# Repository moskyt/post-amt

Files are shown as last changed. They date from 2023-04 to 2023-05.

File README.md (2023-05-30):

# POSTAMT

Darek pro Vlka a Vorsilu k narozeninam 2023.

Obecne: posledni tyden provazela hardwarova dramata a tak je SW mirne nedotazeny. Urceno k libovolnym upravam chovani i implementace podle potreby a aktualnich napadu.

## Hardware

### Komponenty

#### mainboard

Arduino Nano Every (5V)

nevim proc a nemel jsem prostor na dalsi zkoumani, ale pokud je pripojeny zdroj do site, tak se mi nedari pripojit pres usb.

#### zdroj - 5+12

MEANWELL RD 35A
https://www.gme.cz/v/1506286/mean-well-rd-35a-spinany-zdroj-pro-vestavbu-kryty

tepdown z 12 na 8.5v pro tiskarnu
https://www.laskakit.cz/mikro-step-down-menic--nastavitelny

#### bzucak

aktivni 5v bzucak

#### ciselnik

vykuchany rotacni ciselnik z telefonu
https://aukro.cz/ciselnik-telefonu-zcela-funkcni-9x4-cm-7034546220

#### LCD 

znakovy LCD 20x4 s i2c
https://www.laskakit.cz/20x4-lcd-displej-2004-modry-i2c-prevodnik/

#### vaha

trikilogramovy vahovy senzor
https://www.laskakit.cz/guang-ce-yzc-131-vazici-senzor-3kg/
https://www.laskakit.cz/ad-prevodnik-modul-24-bit-2-kanaly-hx711/

#### led displej pro vahu

4-digit 8-segment
https://www.laskakit.cz/hodinovy-displej-0-56--tm1637/

#### RFID ctecka -- RC522 / 13.56 MHz

https://www.laskakit.cz/rfid-ctecka-s-vestavenou-antenou-mfrc-522-rc522/

#### zamek

https://www.laskakit.cz/elektromagneticky-zamek-pro-dvere-12vdc-0-6a/

pres mosfet
https://www.laskakit.cz/pwm-mosfet-modul-lr7843--30vdc-161a/

#### tiskarna

https://www.adafruit.com/product/597

#### klavesnice

NeoKey
https://www.adafruit.com/product/4980

### Zapojeni

#### Piny z Arduina

2+3 - vaha (data, clk)
4 - bzucak
5 - rotacni ciselnik
7+8 - led (clk, data)
9+10 - rfid (ss, rst)
16+17 - tiskarna (rx, tx)
18+19 - I2C (neokey, LCD)
20 - zamek pres mosfet

#### Pripojeni komponent na mainboard

R32-35 vaha[GND,DATA,CLK,VCC]
? bzucak[+,GND]
R27-28 rotacni ciselnik[*,*]
R38-41 led[VCC,GND,DATA,CLK]
L23-20 lcd[GND,VCC,SDA,SCL]
L36-34 tiskarna[?,?,GND]
L45-38 rfid[3v3,?,GND,?,MISO,?,SCK,SS]
L30-27 neokey[VCC,GND,SCL,SDA]

zamek -- do svorkovnice na mosfetu

5v napajeni -- do svorkovnice na mainboardu
12v napajeni -- do wago svorek

#### 12V komponenty

mosfet pro zamek

napajeni pro tiskarnu (stepdown na 8.5VÎ)

## Funkce

### Vaha

po zatizeni se ukaze hmotnost

pokud neprobiha odesilani zasilek, lze tlacitkem vynulovat taru

### Odesilani zasilek

po navazeni vybiram tlacitkem balik nebo dopis

na LCD se mi ukaze pridana zasilka a pocet zasilek

tlacitkem vsechno vyresetuju

tlacitkem zahajim odesilani

po prilozeni karty se vytiskne listecek

### Suplik

po vytoceni kodu 1234 se otevre

zapadka: vzadu shora

automaticke otevirani na odpuzujici se magnety vedlo k tomu, ze se zapadka nedokazala otevrit (tlak zboku - vysoke treni nebo se to rovnou zkrizilo). nestihnul jsem vyzkouset ruzne alternativy, ale mozna by to spravne slaba pruzina nebo spravna dvojice magnetu vyresila.

--- na posledni chvili jsem zkusil dat tam dvojici slabsich magnetu a obecne to funguje skvele, ale uz se mi taky stalo, ze se to odmitlo otevrit. tak nevim, je asi potreba posoudit provozni zkusenost. kdyztak proste staci vyndat jeden magnet a je to. nejaky automatizovany chytroreseni by vyzadovalo koncovej spinac a dat tomu vic pokusu, ale to bylo nad aktualni ramec moznosti.

## Software

jako obvykle to vznikalo v prvni fazi dlouho a v druhe fazi narychlo a urcite nema nikdo nic proti zasadnim i drobnym zmenam.

neni tam asi nic nestandardniho, snad jen ten timer pro asynchronni reseni toho rotacniho ciselniku. 

### Logo Die Post na tiskarnu

pouzil jsem postup z https://learn.adafruit.com/mini-thermal-receipt-printer/bitmap-printing

ten skript je v adresari grafika taky

## Playware

nejaky bizar z aukra

par osvojenych formularu z ceske posty

pokud mi bude sihlpost milostiv, tak https://shop.post.ch/shop/ui/de/geschenke/spielwaren/kinderpost-zubehor/p/507512

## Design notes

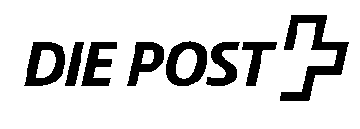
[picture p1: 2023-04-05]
grafika/die_post_360.png

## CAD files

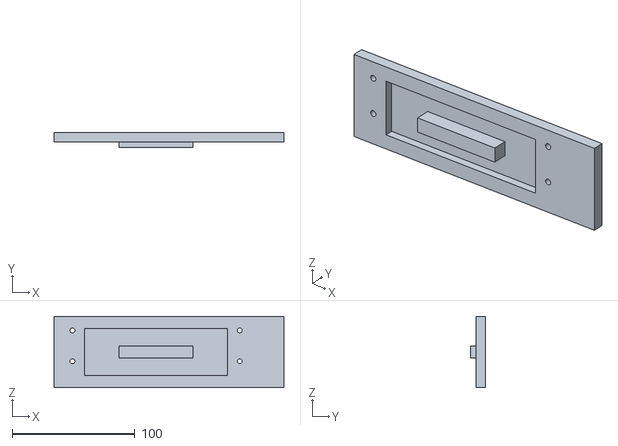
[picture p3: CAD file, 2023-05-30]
grafika/postamt_front_drawer.stl
187.0 x 12.0 x 58.0

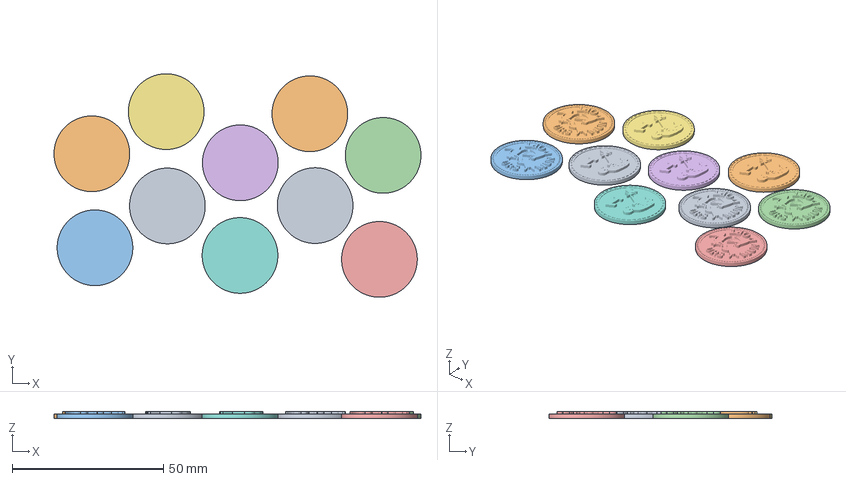
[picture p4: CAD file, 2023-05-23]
grafika/mince v4.3mf
121.2 x 73.8 x 2.20 mm

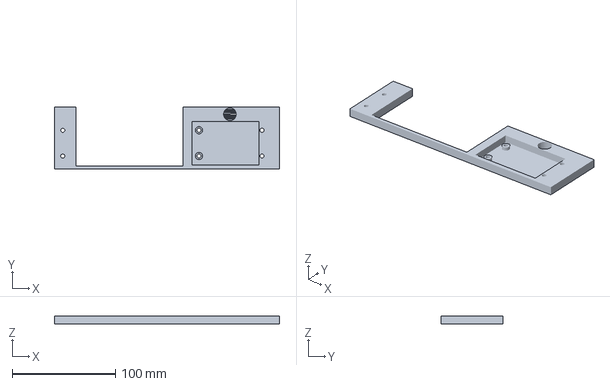
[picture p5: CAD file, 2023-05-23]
grafika/postamt_front_module.3mf
218.0 x 60.0 x 7.50 mm

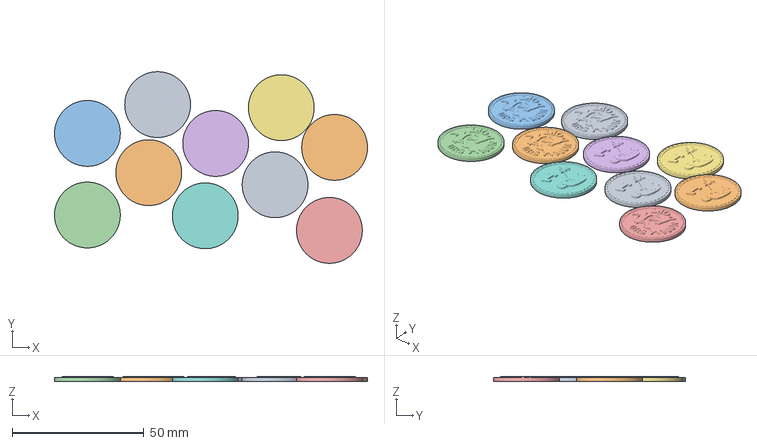
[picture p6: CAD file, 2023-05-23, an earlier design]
grafika/mince v2.3mf
118.9 x 72.8 x 2.00 mm

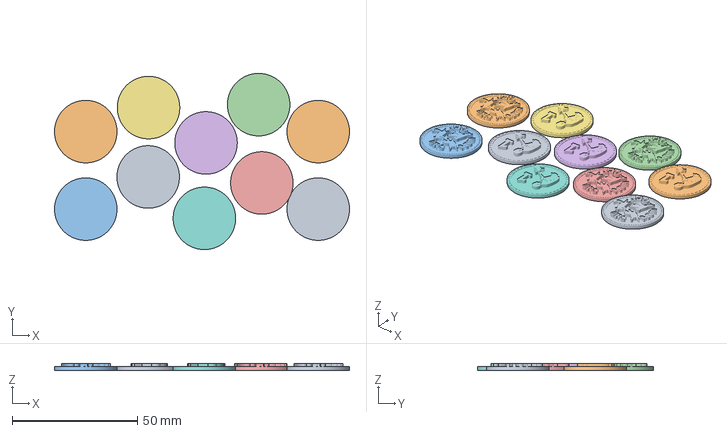
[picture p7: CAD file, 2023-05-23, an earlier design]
grafika/mince v3.3mf
118.0 x 70.5 x 2.60 mm

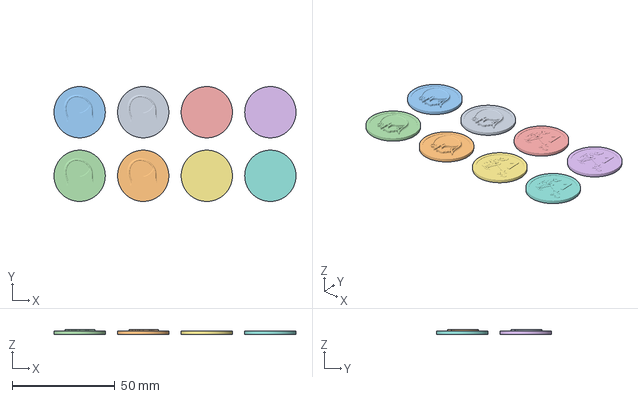
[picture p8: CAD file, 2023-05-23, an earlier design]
grafika/mince v1.3mf
118.0 x 56.0 x 2.20 mm

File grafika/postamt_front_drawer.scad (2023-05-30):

include <bosl2/std.scad>
$fn = 80;

eps = 0.01;

total_z = 7.5;
total_y = 58;
total_x = 187;
roffset_x1 = 36;
roffset_x2 = 172;

printer_x = 103.5;
printer_y = 57;

rfid_up = 13;

difference() {
    cuboid([total_x,total_z,total_y], anchor = BOTTOM+RIGHT+FWD);

    fwd(eps)
    up(rfid_up+1) {

    left(roffset_x1)
    union() {
        up(7.5)
        ycyl(d = 4, l = total_z+2*eps, anchor = FWD);
        up(32.5)
        ycyl(d = 4, l = total_z+2*eps, anchor = FWD);    
    }

    left(roffset_x2)
    union() {
        up(7.5)
        ycyl(d = 4, l = total_z+2*eps, anchor = FWD);
        up(32.5)
        ycyl(d = 4, l = total_z+2*eps, anchor = FWD);
    }
    }

    fwd(eps)
    up(10)
    left(roffset_x1+10)
    cuboid([roffset_x2-roffset_x1-20,total_z-2+eps,total_y-20], anchor = BOTTOM+RIGHT+FWD);

}

back(eps+total_z-2)
left(roffset_x1 + (roffset_x2-roffset_x1)/2)
up(total_y/2)
cuboid([60,10+eps,10], anchor = BACK);

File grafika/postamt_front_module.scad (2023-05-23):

include <bosl2/std.scad>
$fn = 80;

eps = 0.01;

total_z = 7.5;
total_y = 60;

printer_lip_x = 5;
board_left = 16;

printer_x = 103.5;
printer_y = 57;

rfid_up = 14;

difference() {
    union() {
        difference() {
            cuboid([218,total_z,total_y], anchor = BOTTOM+LEFT+FWD);

            right(board_left+printer_lip_x)
            fwd(eps)
            down(eps)
            cuboid([printer_x,total_z+eps*2,printer_y+eps], anchor = BOTTOM+LEFT+FWD);
            
            right(133)
            up(rfid_up)
            back(1)
            cuboid([65,total_z,42], anchor = BOTTOM+LEFT+FWD);
        }    
        right(133+1+6)
        union() {
            up(rfid_up+1+7.5)
            ycyl(d = 7, l = 4, anchor = FWD);
            up(rfid_up+1+32.5)
            ycyl(d = 7, l = 4, anchor = FWD);
        }
    }

    fwd(eps-1)
    right(170)
    up(7)
    ycyl(d = 12.2, l = total_z+2*eps, anchor = FWD);

    fwd(eps)
    right(170)
    up(7)
    intersection() {
       ycyl(d = 12.2, l = total_z+2*eps, anchor = FWD);
       fwd(eps)
        zcopies(2,5)
       cuboid([16,16,1+2*eps], anchor = FWD);

    }

    fwd(eps)
    up(rfid_up+1) {
    right(board_left/2)
    union() {
        up(7.5)
        ycyl(d = 4, l = total_z+2*eps, anchor = FWD);
        up(32.5)
        ycyl(d = 4, l = total_z+2*eps, anchor = FWD);
    }

    right(201)
    union() {
        up(7.5)
        ycyl(d = 4, l = total_z+2*eps, anchor = FWD);
        up(32.5)
        ycyl(d = 4, l = total_z+2*eps, anchor = FWD);
    }

    right(133+1+6)
    union() {
        up(7.5)
        ycyl(d = 4, l = total_z+2*eps, anchor = FWD);
        up(32.5)
        ycyl(d = 4, l = total_z+2*eps, anchor = FWD);
    }
}
}

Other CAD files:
grafika/postamt_front_module.stl

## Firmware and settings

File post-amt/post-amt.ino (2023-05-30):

#include "Adafruit_Thermal.h"
#include "Adafruit_NeoKey_1x4.h"
#include "seesaw_neopixel.h"
#include "SoftwareSerial.h"
#include <Wire.h>
#include <hd44780.h>                      
#include <hd44780ioClass/hd44780_I2Cexp.h>
#include <MFRC522v2.h>
#include <MFRC522DriverSPI.h>
#include <MFRC522DriverPinSimple.h>
#include <MFRC522Debug.h>
#include <HX711_ADC.h>
#include <TM1637Display.h>
#include "die_post_360.h"

//--- pins and adresses

const int I2C_LCD = 0x27;
const int I2C_NEOKEY = 0x30;

const int PIN_LOAD_DATA = 2;
const int PIN_LOAD_CLK = 3;
const int PIN_BEEP = 4;
const int PIN_DIAL = 5;
const int PIN_LED_DATA = 7;
const int PIN_LED_CLK = 8;
const int PIN_RFID_RST = 9;
const int PIN_RFID_SS  = 10;
const int PIN_PRINTER_TX = 16;
const int PIN_PRINTER_RX = 17;
const int PIN_LOCK = 20;
const int PIN_ROTARY = 21;

//--- RFID card ids
const unsigned long int UID_VLK     = 0x9763D21E;
const unsigned long int UID_VORSILA = 0x5B693E3A;

//--- neokey functional assignment
const int BTN_ADD_PARCEL = 0;
const int BTN_ADD_LETTER = 1;
const int BTN_SEND = 2;
const int BTN_RESET = 3;
const int BTN_TARE = 3;

//--- configuration
const float load_cell_cal = 733.0; // this should be acquired from the calibration script; it is available as an example in the HX711_ADC library
const int min_load = 2;
const int scale_zero_weight_timeout = 5000;
const int correct_code = 1234;

//--- hw components

// RFID reader
MFRC522DriverPinSimple ss_pin(PIN_RFID_SS);
SPIClass &spiClass = SPI;
const SPISettings spiSettings = SPISettings(SPI_CLOCK_DIV4, MSBFIRST, SPI_MODE0); 
MFRC522DriverSPI driver{ss_pin, spiClass, spiSettings};
MFRC522 mfrc522{driver};

// LCD display
hd44780_I2Cexp lcd(I2C_LCD);

// LED display
TM1637Display led(PIN_LED_CLK, PIN_LED_DATA);

// neokey 4-button leopard
Adafruit_NeoKey_1x4 neokey;

// 3kg load cell with HX711
HX711_ADC loadcell(PIN_LOAD_DATA, PIN_LOAD_CLK);

//
SoftwareSerial printerSerial(PIN_PRINTER_RX, PIN_PRINTER_TX);
Adafruit_Thermal printer(&printerSerial);

//--- state management

enum shipment_type_ {SHIPMENT_TYPE_NONE, SHIPMENT_TYPE_PARCEL, SHIPMENT_TYPE_LETTER};

enum scale_state_ {SCALE_OFF, SCALE_ON} scale_state;

enum shipping_state_ {SHIPPING_COLLECTION, SHIPPING_CARD, SHIPPING_PRINTING} shipping_state;

int scale_weight = 0;
int shipment_count = 0;
const int max_shipment_count = 5;
int shipment_weight[max_shipment_count];
shipment_type_ shipment_type[max_shipment_count];

// global time at beginning of loop()
unsigned long now = 0;
// flag register of the neokey 
uint8_t buttons = 0;

// timers stuff -- taken from the library

// Select USING_16MHZ     == true for  16MHz to Timer TCBx => shorter timer, but better accuracy
// Select USING_8MHZ      == true for   8MHz to Timer TCBx => shorter timer, but better accuracy
// Select USING_250KHZ    == true for 250KHz to Timer TCBx => shorter timer, but better accuracy
// Not select for default 250KHz to Timer TCBx => longer timer,  but worse accuracy
#define USING_16MHZ     false
#define USING_8MHZ      false
#define USING_250KHZ    false

// Select the timers you're using, here ITimer1
#define USE_TIMER_0     false
#define USE_TIMER_1     true
#define USE_TIMER_2     false
#define USE_TIMER_3     false

#include "megaAVR_TimerInterrupt.h"

// --- dial stuff
// last value read
int dialLastVal = -1;
// timer/counter
int dialCount = 0;
// current number being read
int dialBuffer = 0;
// number of digits in code
const int dialNMax = 4;
// current code read
int dialNumber[dialNMax] = {0,0,0,0};
// current digit
int dialPtr = 0;

// what is available after init
// the idea here is that if neokey is not connected, any call results in reset
bool neokey_available = false;
bool rfid_available = false;

// what is currently read
// remember that 0 is a valid value for dial...
int dial_read = -1;
unsigned long card_read = -1;

// what is shown and when
int show_dial = -1;
unsigned long show_card = 0;
unsigned long int show_card_at = 0;
unsigned long int show_dial_at = 0;
const int show_delay = 10000; // actual ms

void loop() {

  now = millis();

  // read keyboard status
  if (neokey_available)
    buttons = neokey.read();

  // flag to show if any of the keyboard data was set
  // give me credit for this not being a global variable
  bool any_info_neo = false;
  if (neokey_available)
    for (uint16_t i=0; i<neokey.pixels.numPixels(); i++) 
      neokey.pixels.setPixelColor(i, 0x000000);

  if (rfid_available) read_rfid();
  display_scale_led();
  get_weight_from_scale();

  // waiting for card before sending?
  if (shipping_state == SHIPPING_CARD) 
    if ( (card_read == UID_VLK) || (card_read == UID_VORSILA) ) 
      print_shipment(card_read);

  // disable ux if printing the receipt
  if (neokey_available)
  if (shipping_state == SHIPPING_PRINTING) {    
    any_info_neo = true;
    for (uint16_t i=0; i<neokey.pixels.numPixels(); i++) 
      neokey.pixels.setPixelColor(i, 0xFF8888);    
  }

  if (shipment_count == 0)
    // allow tare setting if no shipping is in progress
    handle_tare(any_info_neo);
  else
    // handle finalization of shipping process (reset or proceed with sending)
    reset_or_send(any_info_neo);  

  // process adding a new item
  add_shipments(any_info_neo);

  // (de)queue other info for show
  if (show_dial > 0) {
    if (show_dial_at + show_delay < now) {
      show_dial = -1;
      show_dial_at = 0;
    }
  } 
  if (dial_read >= 0 && show_dial != dial_read) {
    show_dial = dial_read;
    show_dial_at = now;
  }
  if (show_card > 0) {
    if (show_card_at + show_delay < now) {
      show_card = 0;
      show_card_at = 0;
    }
  } 
  if (card_read > 0 && show_card != card_read) {
    show_card = card_read;
    show_card_at = now;
  }


  if (shipment_count > 0 || show_card_at > 0 || show_dial_at > 0) 
    lcd.backlight();

  if (show_card_at == now && (show_dial_at == 0 || show_card_at > show_dial_at)) {
    lcd.setCursor(0,2);
    lcd.print(F("KARTA:               "));
    lcd.setCursor(0,3);
    if (show_card == UID_VORSILA) 
      lcd.print(F("VORSILA             "));
    else if (show_card == UID_VLK) 
      lcd.print(F("VLK                 "));
    else
      lcd.print(show_card, HEX);
  } else if (show_dial_at == now) {
    lcd.setCursor(0,2);
    lcd.print(F("KOD ZAMKU:"));
    lcd.setCursor(0,3);
    if (show_dial < 1000) lcd.print(F("0"));
    if (show_dial < 100) lcd.print(F("0"));
    if (show_dial < 10) lcd.print(F("0"));
    lcd.print(show_dial);
  }
  
  // clear shipping info
  if (shipment_count == 0) lcd_clear_top();
  // clear card/dial info
  if ((show_card_at == 0) && (show_dial_at == 0)) lcd_clear_bottom();

  // shut off lcd if there is nothing going on
  if ( (shipment_count == 0) && (show_dial_at == 0) && (show_card_at == 0) ) {
    lcd.noBacklight();
    lcd.clear();
  }

  if (neokey_available) {
    // show pixels: either just use pale white or whatever was set by the ux
    if (!any_info_neo) 
      for (uint16_t i=0; i<neokey.pixels.numPixels(); i++) 
        neokey.pixels.setPixelColor(i, 0x333333);
    neokey.pixels.show();    
  }

  // unlock
  if (dial_read >= 0) {
    Serial.print(F("dial: "));
    Serial.println(dial_read);
    if (dial_read == correct_code) {
      dial_read = -1;
      Serial.println(F("Unlocking."));
      digitalWrite(PIN_LOCK, HIGH);
      delay(1000);
      digitalWrite(PIN_LOCK, LOW);
    } else {
      Serial.println(F("Code not correct."));
      beep1(500);
    }
    dial_read = -1;
  }

  // any delay is inherently bad, maybe we can refactor this to use timers. but...
  delay(50);
}

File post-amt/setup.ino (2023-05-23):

void setup() {
  // ---
  Serial.begin(115200);
  while (! Serial) delay(10);
  Serial.println(F("PostAmt HELO\n"));  

  // --- lock
  pinMode(PIN_LOCK, OUTPUT);
  digitalWrite(PIN_LOCK, LOW);
  
  // --- dial
  pinMode(PIN_DIAL, INPUT_PULLUP);

  // ---
  Serial.println(F("Init LCD ... "));  
  int status = lcd.begin(20, 4);
  if(status) {
    Serial.println(F("FAILED."));
  } else {
    Serial.println(F("OK."));  
  }

  lcd.setCursor(0,0);
  lcd.print(F("PostAmt"));
  lcd.setCursor(0,1);
  lcd.print(F("======="));
  delay(2000);

  // ---
  lcd.setCursor(0,3);
  lcd.print(F("(klavesnice)        "));
  Serial.println(F("Init NeoKey ... "));  
  if (!neokey.begin(I2C_NEOKEY)) {
    Serial.println(F("FAILED."));
    neokey_available = false;
  } else {
    Serial.println(F("OK."));  
    neokey_available = true;
  }

  neokey.pixels.setPixelColor(0, 0xFF0000);
  neokey.pixels.setPixelColor(1, 0xFFFF00);
  neokey.pixels.setPixelColor(2, 0x00FF00);
  neokey.pixels.setPixelColor(3, 0x0000FF);
  neokey.pixels.show();
  delay(1000);

  // ---
  lcd.setCursor(0,3);
  lcd.print(F("(vaha)           "));
  Serial.println(F("Init LED ... "));  
  led.setBrightness(0x0f);
  Serial.println(F("OK."));  
  uint8_t data[] = { 0xff, 0xff, 0xff, 0xff };
  led.setSegments(data);

  // ---
  Serial.println(F("Init load cell ... "));  
  loadcell.begin();
  loadcell.start(2000, true);
  if (loadcell.getTareTimeoutFlag()) {
    Serial.println(F("FAILED"));
  } else {
    loadcell.setCalFactor(load_cell_cal);
    Serial.println(F("OK."));  
  }

  // ---
  Serial.println(F("Init beeper..."));
  pinMode(PIN_BEEP, OUTPUT);
  digitalWrite(PIN_BEEP, LOW);
  Serial.println(F("OK."));  
  
  // ---
  lcd.setCursor(0,3);
  lcd.print(F("(ctecka karet)     "));
  Serial.println(F("Init RFID ... "));  
  /*
  I had to comment this out because it made it non worky.
  But I am not happy about it at all.

  pinMode(PIN_RFID_RST, OUTPUT);
  digitalWrite(PIN_RFID_RST, LOW);
  delay(500);
  digitalWrite(PIN_RFID_RST, HIGH);
  delay(500);
  */
  mfrc522.PCD_Init();
  MFRC522Debug::PCD_DumpVersionToSerial(mfrc522, Serial);
  if (mfrc522.PCD_PerformSelfTest()) {
    rfid_available = true;
    Serial.println(F("OK."));  
  } else {
    rfid_available = false;
    Serial.println(F("FAILED."));  
  }


  // ---
  lcd.setCursor(0,3);
  lcd.print(F("(tiskarna)     "));
  Serial.println(F("Init printer ... "));  

  printerSerial.begin(19200);
  printer.begin();        
  printer.setFont('B');
  printer.feed(1);
  printer.sleep();      // Tell printer to sleep

  delay(2000);

  // ---
  scale_state = SCALE_OFF;
  scale_weight = 0;

  shipping_state = SHIPPING_COLLECTION;
  shipment_count = 0;

  neokey.pixels.setPixelColor(0, 0x333333);
  neokey.pixels.setPixelColor(1, 0x333333);
  neokey.pixels.setPixelColor(2, 0x333333);
  neokey.pixels.setPixelColor(3, 0x333333);
  neokey.pixels.show();

  // --- dial timer
	ITimer1.init();
  if (ITimer1.attachInterruptInterval(10, dialHandler))
    Serial.println(F("Timer init OK."));
  else
    Serial.println(F("Can't set ITimer1. Select another freq. or timer"));

  lcd.setCursor(0,3);
  lcd.print(F("muzes uradovat!   "));
  Serial.println(F("Init completed."));  

  // ---
  delay(2000);
  lcd.clear();
  lcd.noBacklight();  

}

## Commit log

2023-05-23 uncountable updates
    [mince v1.3mf, mince v2.3mf, mince v3.3mf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]
2023-05-30 uklid v grafice, doplneni dokumentace, post-last-minute mirny refactoring
    [postamt_front_drawer.scad, postamt_front_drawer.stl]
